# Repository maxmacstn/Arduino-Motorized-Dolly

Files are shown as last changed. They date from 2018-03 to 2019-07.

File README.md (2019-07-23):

# Arduino-Motorized-Dolly
Convert generic camera dolly rail into controllable motorized dolly.

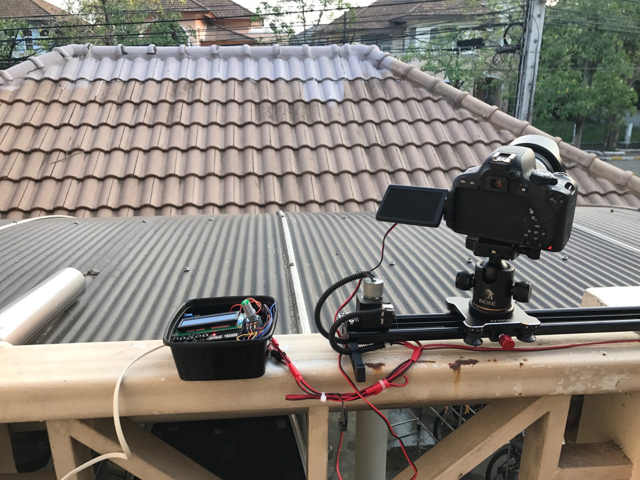
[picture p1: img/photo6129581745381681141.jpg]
Arduino Dolly


## Features
- 5v powerbank input (Portable!)
- Adjustable speed.
- Video mode (Continuous movement)
- TimeLapse mode with camera shutter trigger.
- Can be set Timelapse delay time (time for camera to save image between shot), Motor position (Left or right of the controller) and Time until display is going to dim. Those are available in Settings menu and the configuration will be stored in the EEPROM which means that configuration still remains after power lost.

## Main Components
1. Andoer 80cm / 32" 4 Bearings Camera Slider
2. Arduino Mega 2560
3. Gear motor 12v 50RPM
4. Arduino Modules
    1. L298N H-Bridge motor driver
    2. LCD Keypad shield
    3. DC-to-DC Step Up XL6009
    4. Limit switch ×2
5. Belt components
    1. timing GT2 belt width 6mm
    2. Timing Pulley 20 ฟัน 2GT 
    3. Pulley Wheel 20 ฟัน 2GT
    4. Timing Belt Fixing Clamp 9*40mm
6. Shutter trigger components
    1. NPN Transistor BC547
    2. Resistor 1K Ω
    3. 2.5mm female headphone jack

## Schematic
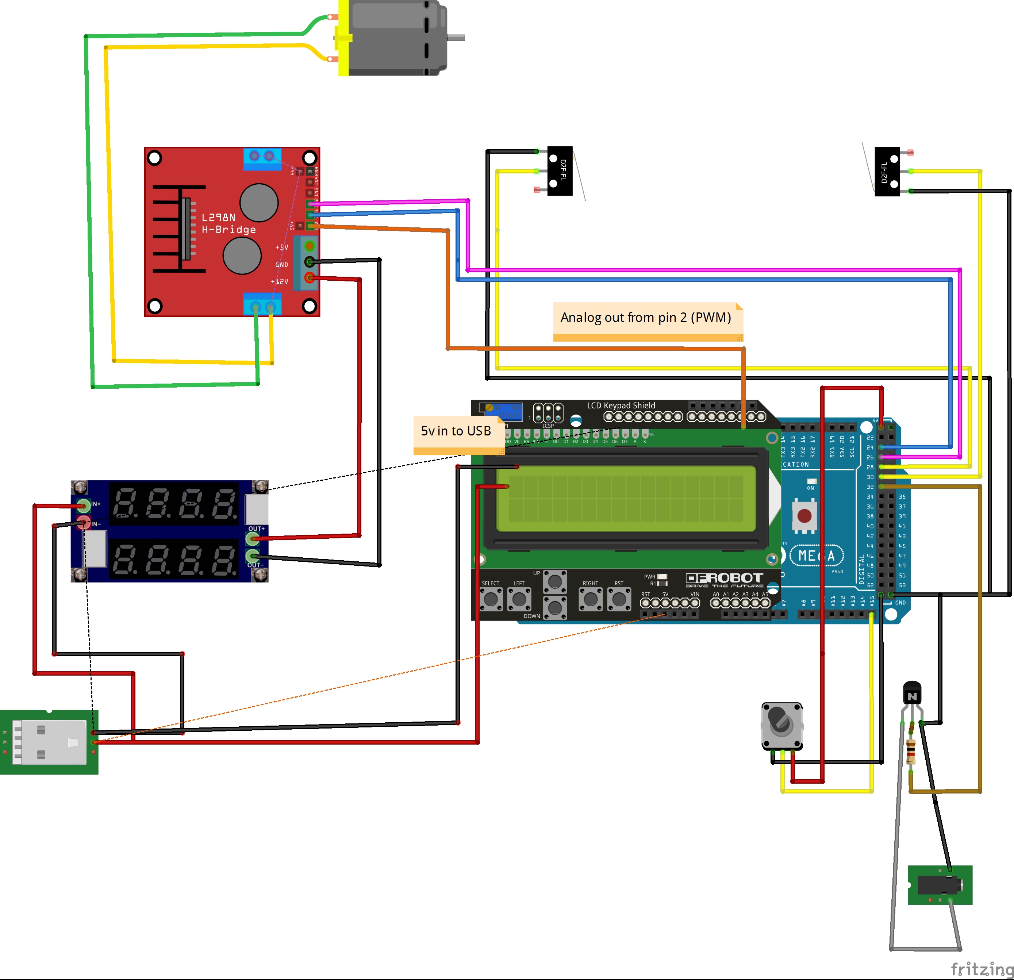
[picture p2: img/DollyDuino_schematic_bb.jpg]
Schematic

 **Pins** (Pin number : variable name - Description)
 - 2 : enA - PWM Motor control 
 - 24 : in1 - Motor rotational  control 1
 - 26 : in2 - Motor rotational control 2
 - 28 : limSW_L - Left limit switch
 - 30 : limSW_R - Right limit switch
 - 32 : shutter - Camera shutter trigger pin
 Those below pins are connected via LCD Keypad shield
  - 0 : btnRIGHT  
  - 1 : btnUP 
  - 2 : btnDOWN 
  - 3 : btnLEFT
  - 4 :btnSELECT
  - 5 : btnNONE 
  - 10 : brightnessPin - PWM-controlled brightness of LCD Backlight

## Dependencies
- LiquidCrystal.h
- EEPROM.h

## Link
- [Youtube Link](https://youtu.be/vfO5Gkq3VD4)
- [Blog(Thai)](https://maxmacstn.wordpress.com/2018/03/09/dollyduino/)

## V.2 Update
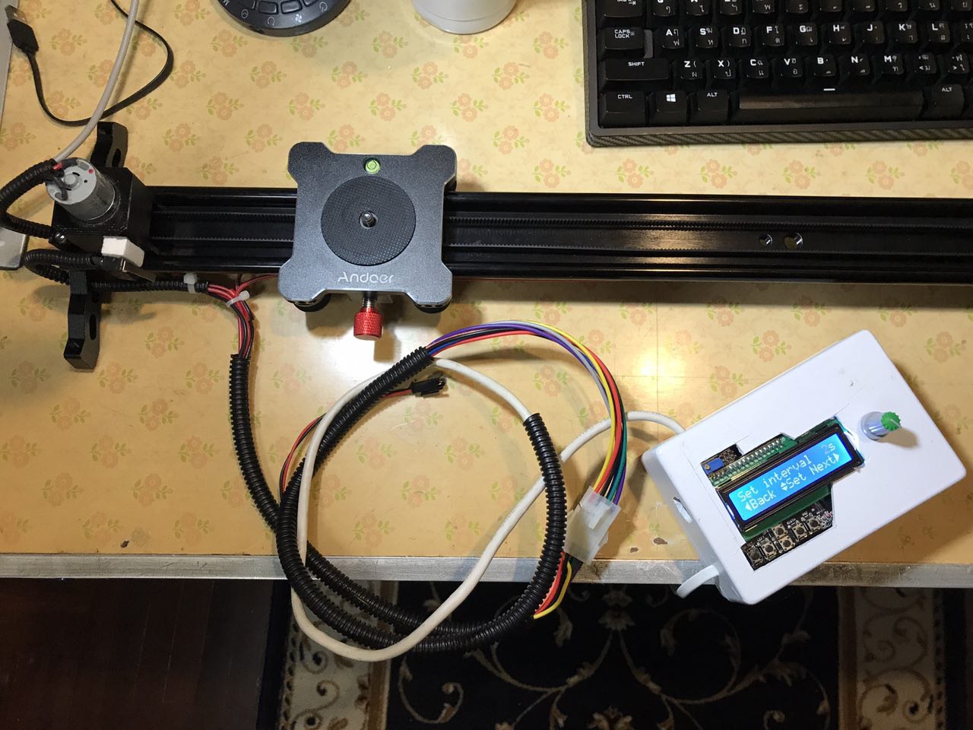
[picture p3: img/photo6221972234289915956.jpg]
Arduino Dolly V.2


-	New nice and tidy Arduino enclosure ([Box from FutureKit : Size FB-04](https://www.futurekit.com/product/25654/fb04))
  You can see how all of the components are perfectly fit in that box from [here](https://github.com/maxmacstn/Arduino-Motorized-Dolly/blob/master/img/photo6221972234289915957.jpg)
-	9 Pins connector, really convenient! 
-	Software upgrade.

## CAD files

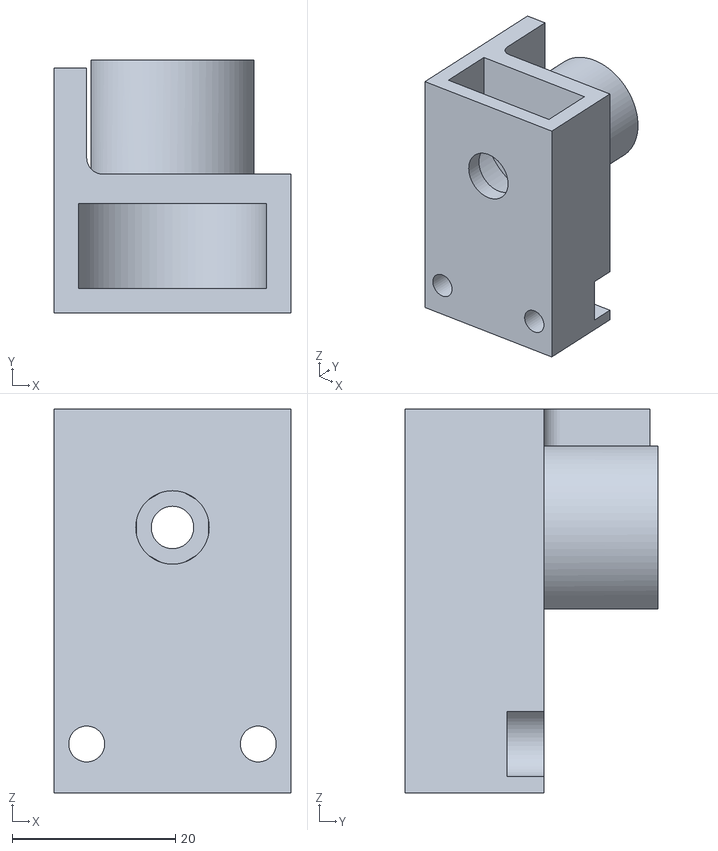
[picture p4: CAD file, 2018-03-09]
3D Files/Belt_holder.stl
29.0 x 31.0 x 47.0

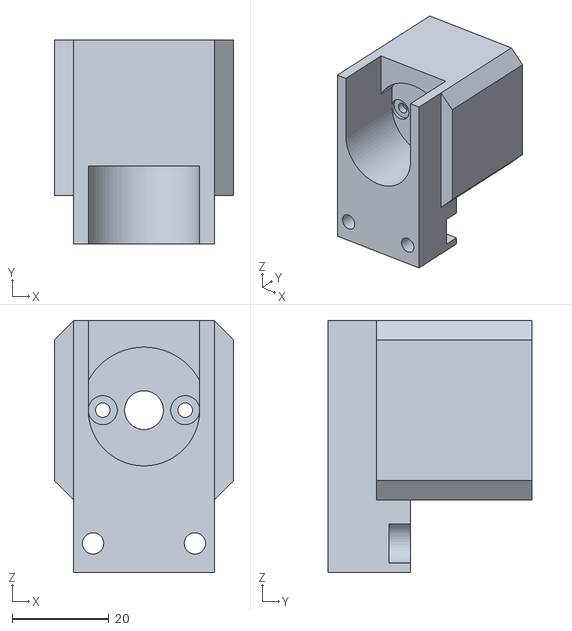
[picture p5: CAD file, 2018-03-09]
3D Files/Motor_holder.stl
37.0 x 42.0 x 52.0

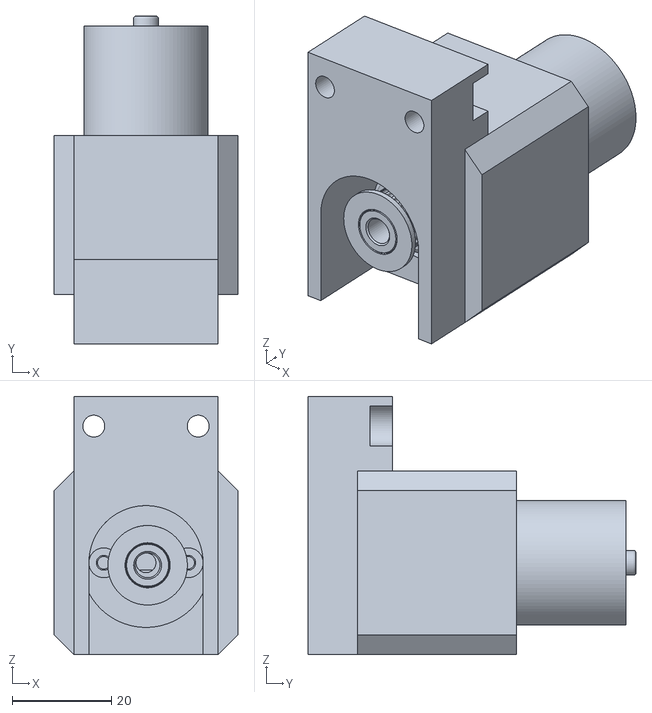
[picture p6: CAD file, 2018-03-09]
3D Files/Motor_holder_with_motor.stl
37.0 x 66.0 x 52.0

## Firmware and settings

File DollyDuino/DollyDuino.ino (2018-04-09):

/**
    @file    DollyDuino
    @author  Sitinut Waisara (maxmacstn)
    @date    April,7 2018
    @version 2.0

    Automated camera dolly control using Arduino.
    https://github.com/maxmacstn/Arduino-Motorized-Dolly
    https://maxmacstn.wordpress.com/2018/03/09/dollyduino/


*/


#include <LiquidCrystal.h>
#include <EEPROM.h>

LiquidCrystal lcd(8, 9, 4, 5, 6, 7);

#define enA 2                       //PWM Motor control
#define in1 24                      //Motor rotational control1
#define in2 26                      //Motor rotational control2
#define limSW_L 28                  //Left limit switch
#define limSW_R 30                  //Right limit switch
#define shutter 32                  //Camera shutter trigger pin
#define btnRIGHT  0 
#define btnUP     1
#define btnDOWN   2
#define btnLEFT   3
#define btnSELECT 4
#define btnNONE   5
#define brightnessPin 10            //LCD Brightness control (Connected from the LCD Keypad shield)


const char* menuItems[] = {"     VIDEO             ", "   TIMELAPSE           ", "    SETTINGS   "};
const unsigned int menuItemsNumber = 3;
const unsigned int sleepTime[] = {0, 10, 30, 120, 300};
unsigned long lastActiveTime = 0;
byte lastPotValue = 255;
byte currentBrightness = 255;
byte motorDir = 0;     // positive = motor is on the left of the controller
byte cameraDelay = 0;  //camera delay between shots (Seconds)
byte dimChoice = 0;    //choice of time until screen was dim.

byte updn_arrow[] = {
  B00100,
  B01110,
  B11111,
  B00000,
  B11111,
  B01110,
  B00100,
  B00000
};

byte left_arrow[] = {

  B00010,
  B00110,
  B01110,
  B11110,
  B01110,
  B00110,
  B00010,
  B00000
};

byte right_arrow[] = {
  B10000,
  B11000,
  B11100,
  B11110,
  B11100,
  B11000,
  B10000,
  B00000
};

byte move_left[] = {
  B00010,
  B00100,
  B01000,
  B10000,
  B01000,
  B00100,
  B00010,
  B00000
};

byte move_right[] = {
  B01000,
  B00100,
  B00010,
  B00001,
  B00010,
  B00100,
  B01000,
  B00000
};



// define some values used by the panel and buttons
int lcd_key     = 0;
int adc_key_in  = 0;
volatile int rotDirection = 0;
int pressed = false;

// read the buttons
int read_LCD_buttons()
{
  adc_key_in = analogRead(0);      // read the value from the sensor
  // my buttons when read are centered at these valies: 0, 144, 329, 504, 741
  // we add approx 50 to those values and check to see if we are close
  if (adc_key_in > 1000) return btnNONE; // We make this the 1st option for speed reasons since it will be the most likely result
  // For V1.1 us this threshold
  resetDisplaySleep();

  if (adc_key_in < 50)   return btnRIGHT;
  if (adc_key_in < 250)  return btnUP;
  if (adc_key_in < 450)  return btnDOWN;
  if (adc_key_in < 650)  return btnLEFT;
  if (adc_key_in < 850)  return btnSELECT;

  return btnNONE;  // when all others fail, return this...
}

void video_mode() {
  lcd.clear();
  lcd.setCursor(3, 0);
  lcd.print("Speed");
  lcd.setCursor(0, 1);
  lcd.write((byte)0);
  lcd.setCursor(1, 1);
  lcd.print("stop");

  resetDisplaySleep();
  checkDisplaySleep();
  bool dir;

  while (1) {

    int potValue = analogRead(A15); // Read potentiometer value
    int pwmOutput = map(potValue, 0, 1023, 0 , 255); // Map the potentiometer value from 0 to 255
    int pwmPercent = map(potValue, 0, 1023, 0, 100); // Map pot to percent for display
    Serial.println(potValue);
    analogWrite(enA, pwmOutput); // Send PWM signal to L298N Enable pin

    // Check limit switch - Debounce
    if (!digitalRead(limSW_L)) {
      rotDirection = 1;
    }
    if (!digitalRead(limSW_R)) {
      rotDirection = 0;
    }
    if (read_LCD_buttons() == btnLEFT) {
      digitalWrite(in1, LOW);
      digitalWrite(in2, LOW);
      lcd.clear();
      return;
    }
    if (read_LCD_buttons() == btnSELECT) {
      while (read_LCD_buttons() == btnSELECT) {}
      rotDirection = !rotDirection;
    }
    delay(20);
    // If button is pressed - change rotation direction
    if (rotDirection == 0) {
      digitalWrite(in1, HIGH);
      digitalWrite(in2, LOW);
      delay(20);
    }
    // If button is pressed - change rotation direction
    if (rotDirection == 1) {
      digitalWrite(in1, LOW);
      digitalWrite(in2, HIGH);
      delay(20);
    }

    //Update LCD
    if (pwmPercent >= 100) {
      lcd.setCursor(9, 0);
      lcd.print(pwmPercent);
    }
    else if (pwmPercent >= 10) {
      lcd.setCursor(9, 0);
      lcd.print(" ");
      lcd.setCursor(10, 0);
      lcd.print(pwmPercent);

    } else {
      lcd.setCursor(9, 0);
      lcd.print("  ");
      lcd.setCursor(11, 0);
      lcd.print(pwmPercent);
    }

    lcd.setCursor(12, 0);
    lcd.print("%");

    lcd.setCursor(0, 0);
    lcd.print("   ");
    lcd.setCursor(13, 0);
    lcd.print("   ");

    //Arrow animation speed.
    int anim_shift = millis() / 1000 % 3;

    if (pwmPercent >= 90) {
      anim_shift = millis() / 500 % 3;
    }

    if (pwmPercent <= 40) {
      anim_shift = millis() / 1500 % 3;
    }
    if (pwmPercent <= 10) {
      anim_shift = millis() / 2500 % 3;
    }

    dir = rotDirection;
    if (motorDir)
      dir = !dir;

    if (!dir) {    //Motor is on the left
      lcd.setCursor(2 - anim_shift, 0);
      lcd.write((byte)3);
    }
    else {
      lcd.setCursor(13 + anim_shift, 0);
      lcd.write((byte)4);
    }

    checkDisplaySleep();

  }
}

//Load user-saved settings from EEPROM into global variable
void loadSaveData() {
  byte loadedMotorDir = EEPROM.read(0);
  byte loadedCameraDelay = EEPROM.read(1);
  byte loadedDimChoice = EEPROM.read(2);

  // Reset EEPROM Value to 0 if the loaded value is not valid.
  if ( loadedMotorDir > 1) {
    loadedMotorDir = 0;
    EEPROM.write(0, 0);
  }
  if ( loadedCameraDelay > 20) {
    loadedCameraDelay = 0;
    EEPROM.write(1, 0);
  }

  if ( loadedDimChoice > 4) {
    loadedDimChoice = 0;
    EEPROM.write(2, 0);
  }

  motorDir = loadedMotorDir;
  cameraDelay = loadedCameraDelay;
  dimChoice = loadedDimChoice;
}

void setup() {
  pinMode(enA, OUTPUT);
  pinMode(in1, OUTPUT);
  pinMode(in2, OUTPUT);
  pinMode(shutter, OUTPUT);

  // Init Limit sensor and set built-in pullup
  pinMode(limSW_L, INPUT);
  pinMode(limSW_R, INPUT);
  digitalWrite(limSW_L, HIGH);
  digitalWrite(limSW_R, HIGH);

  // Set initial rotation direction
  digitalWrite(in1, LOW);
  digitalWrite(in2, HIGH);

  pinMode(brightnessPin, OUTPUT);
  digitalWrite(brightnessPin, HIGH);

  //Serial.begin(9600);

  //Create custom characters
  lcd.createChar(0, left_arrow);
  lcd.createChar(1, right_arrow);
  lcd.createChar(2, updn_arrow);
  lcd.createChar(3, move_left);
  lcd.createChar(4, move_right);

  //init led screen
  lcd.begin(16, 2);              // start the library
  lcd.clear();
  lcd.setCursor(0, 0);
  lcd.print(" DollyDuino 2.0"); // print a Welcome message
  lcd.setCursor(3, 1);
  lcd.print("Starting...."); // print a Welcome message
  loadSaveData();
  delay(1000);
}

void loop() {
  lcd.clear();
  lcd.setCursor(3, 0);
  lcd.print("Main Menu");
  int currentMenu = 0;
  lcd.setCursor(0, 1);
  lcd.print(menuItems[0]);
  Serial.println("MainLoop");
  lcd.setCursor(15, 1);
  lcd.write((byte)1);
  resetDisplaySleep();
  while (1) {
    if (read_LCD_buttons() == btnRIGHT && currentMenu != menuItemsNumber - 1 ) {
      while (read_LCD_buttons() == btnRIGHT) {};
      update_lcd_menu(currentMenu + 1, true);
      currentMenu++;

    }
    if (read_LCD_buttons() == btnLEFT && currentMenu != 0) {
      while (read_LCD_buttons() == btnLEFT) {};
      update_lcd_menu(currentMenu - 1, false);
      currentMenu--;
    }
    if (read_LCD_buttons() == btnSELECT) {
      while (read_LCD_buttons() == btnSELECT) {};
      switch (currentMenu) {
        case 0: video_mode(); break;
        case 1: time_lapse(); break;
        case 2: setting_page(); break;
      }
      break;
    }

    checkDisplaySleep();

  }




}

void update_lcd_menu(int targetMenu, boolean isIncrement) {
  checkDisplaySleep();

  int scroll_speed = 10;

  //Text scroll animation
  if (isIncrement == true) {                  //Right to left
    //Move previous text out of screen
    for (int i = 0; i > -16; i--) {

      lcd.setCursor(0, 1);
      //lcd.print("                ");
      lcd.setCursor(i, 1);
      lcd.print(menuItems[targetMenu - 1]);
      delay(scroll_speed);
    }
    for (int i = 16; i >= 0; i--) {
      lcd.setCursor(0, 1);
      //lcd.print("                ");
      lcd.setCursor(i, 1);
      lcd.print(menuItems[targetMenu]);
      delay(scroll_speed);
    }
  }
  else {                                      //Left to right
    //Move previous text out of screen
    for (int i = 0; i < 16; i++) {
      lcd.setCursor(0, 1);
      //lcd.print("                ");
      lcd.setCursor(i, 1);
      lcd.print(menuItems[targetMenu + 1]);
      delay(scroll_speed);
    }
    for (int i = -16; i <= 0; i++) {
      lcd.setCursor(0, 1);
      //lcd.print("                ");
      lcd.setCursor(i, 1);
      lcd.print(menuItems[targetMenu]);
      delay(scroll_speed);
    }

  }

  //Draw arrow
  if (targetMenu != 0) {
    lcd.setCursor(0, 1);
    lcd.write((byte)0);
  }
  if (targetMenu != menuItemsNumber - 1) {
    lcd.setCursor(15, 1);
    lcd.write((byte)1);
  }

  return;

}


void time_lapse() {
  resetDisplaySleep();
  checkDisplaySleep();
  lcd.clear();
  byte int_sec = 1;
  int step_sec = 500;
  while (1) {
    lcd.setCursor(0, 0);
    lcd.print("Set interval");
    lcd.setCursor(15, 0);
    lcd.print("s");
    lcd.setCursor(0, 1);
    lcd.write((byte)0);
    lcd.setCursor(1, 1);
    lcd.print("Back");

    lcd.setCursor(6, 1);
    lcd.write((byte)2);
    lcd.setCursor(7, 1);
    lcd.print("Set");

    lcd.setCursor(11, 1);
    lcd.print("Next");
    lcd.setCursor(15, 1);
    lcd.write((byte)1);
    boolean value_update = false;
    if (read_LCD_buttons() == btnUP) {
      while (read_LCD_buttons() == btnUP) {}
      if (int_sec < 100) {
        int_sec++;
        value_update = true;
      }
    }
    if (read_LCD_buttons() == btnDOWN) {
      while (read_LCD_buttons() == btnDOWN) {}
      if (int_sec > 1) {
        int_sec--;
        value_update = true;
      }
    }
    if (read_LCD_buttons() == btnLEFT) {
      lcd.clear();
      return;
    }

    //Blink and update LCD
    if (millis() % 1000 > 500 || value_update == true) {
      if (int_sec >= 10) {
        lcd.setCursor(13, 0);
      }
      else {
        lcd.setCursor(13, 0);
        lcd.print(" ");
        lcd.setCursor(14, 0);
      }
      lcd.print(int_sec);
    }
    else {
      lcd.setCursor(13, 0);
      lcd.print("  ");
    }

    //Continue to step 2
    if (read_LCD_buttons() == btnRIGHT) {
      lcd.clear();
      while (read_LCD_buttons() == btnRIGHT) {};
      while (1) {
        lcd.setCursor(0, 0);
        lcd.print("Set move");
        lcd.setCursor(14, 0);
        lcd.print("ms");
        lcd.setCursor(0, 1);
        lcd.write((byte)0);
        lcd.setCursor(1, 1);
        lcd.print("Back");

        lcd.setCursor(6, 1);
        lcd.write((byte)2);
        lcd.setCursor(7, 1);
        lcd.print("Set");

        lcd.setCursor(12, 1);
        lcd.print("Run");
        lcd.setCursor(15, 1);
        lcd.write((byte)1);
        boolean value_update = false;
        if (read_LCD_buttons() == btnUP) {
          while (read_LCD_buttons() == btnUP) {}
          if (step_sec < 9000) {
            step_sec += 100;
            value_update = true;
          }
        }
        if (read_LCD_buttons() == btnDOWN) {
          while (read_LCD_buttons() == btnDOWN) {}
          if (step_sec > 100) {
            step_sec -= 100;
            value_update = true;
          }
        }

        //Blink and update LCD
        if (millis() % 1000 > 500 || value_update == true) {
          if (step_sec >= 1000) {
            lcd.setCursor(10, 0);
          }
          else {
            lcd.setCursor(10, 0);
            lcd.print("   ");
            lcd.setCursor(11, 0);
          }
          lcd.print(step_sec);
        }
        else {
          lcd.setCursor(10, 0);
          lcd.print("    ");
        }
        if (read_LCD_buttons() == btnLEFT) {
          while (read_LCD_buttons() == btnLEFT) {};
          lcd.clear();
          break;
        }
        if (read_LCD_buttons() == btnRIGHT) {
          lcd.clear();
          do_timeLapse(int_sec + cameraDelay, step_sec);
        }
        checkDisplaySleep();

      }
      checkDisplaySleep();

    }//End step2
    checkDisplaySleep();
  }

}

void do_timeLapse(char int_sec, int step_sec) {
  unsigned long startShootMillis = 0;
  unsigned long startMoveMillis = 0;
  boolean isShot = false;
  boolean isShooting = false;
  boolean isFirstEnter = true;
  unsigned int shotCount = 0;
  lcd.setCursor(0, 0);
  lcd.print("TimeLapse");
  lcd.setCursor(13, 0);
  lcd.print("img");
  lcd.setCursor(0, 1);
  lcd.write((byte)0);
  lcd.setCursor(1, 1);
  lcd.print("Stop");

  resetDisplaySleep();
  checkDisplaySleep();

  while (1) {
    lcd.setCursor(10, 0);
    lcd.print(shotCount);
    int potValue = analogRead(A15); // Read potentiometer value
    int pwmOutput = map(potValue, 0, 1023, 0 , 255); // Map the potentiometer value from 0 to 255
    unsigned long currentMillis = millis();
    Serial.println(potValue);
    analogWrite(enA, pwmOutput); // Send PWM signal to L298N Enable pin

    // Check limit switch - Debounce
    if (!digitalRead(limSW_L)) {
      rotDirection = 1;
    }
    if (!digitalRead(limSW_R)) {
      rotDirection = 0;
    }
    if (read_LCD_buttons() == btnLEFT) {
      digitalWrite(in1, LOW);
      digitalWrite(in2, LOW);
      lcd.clear();
      return;
    }
    Serial.print("startShootMillis = ");
    Serial.println(startShootMillis);
    Serial.print("startMoveMillis = ");
    Serial.println(startMoveMillis);
    Serial.print("CurrentMillis = ");
    Serial.println(currentMillis);

    // exceed delay time of move
    if (currentMillis - startMoveMillis >= step_sec) {
      Serial.println("Exceed move time");
      digitalWrite(in1, LOW);
      digitalWrite(in2, LOW);
      if (isFirstEnter == true) {
        startShootMillis = millis();
        currentMillis = millis();
        isFirstEnter = false;
      }
      // exceed delay time of shooting
      if (currentMillis - startShootMillis  >= int_sec * 1000) {
        startMoveMillis = millis();
        Serial.println("Exceed shoot time ...................");
        Serial.println(startShootMillis -  currentMillis);
        isFirstEnter = true;
        isShot = true;

      } else if (isShot == true) {
        delay(100);
        digitalWrite(shutter, HIGH);
        delay(100);
        digitalWrite(shutter, LOW);
        isShot = false;
        shotCount++;
      }

    } else {  // Move motor
      if (rotDirection == 0) {
        digitalWrite(in1, HIGH);
        digitalWrite(in2, LOW);
        // delay(20);
      }
      // If button is pressed - change rotation direction
      if (rotDirection == 1) {
        digitalWrite(in1, LOW);
        digitalWrite(in2, HIGH);
        //delay(20);
      }

      checkDisplaySleep();
    }
    checkDisplaySleep();
  }
}

void setting_page() {
  lcd.clear();
  byte newMotorDir = motorDir;
  while (1) {
    lcd.setCursor(0, 0);
    lcd.print("Motor pos.");




    lcd.setCursor(0, 1);
    lcd.write((byte)2);
    lcd.setCursor(1, 1);
    lcd.print("Set");

    lcd.setCursor(11, 1);
    lcd.print("Next");
    lcd.setCursor(15, 1);
    lcd.write((byte)1);
    boolean value_update = false;
    if (read_LCD_buttons() == btnUP || read_LCD_buttons() == btnDOWN ) {
      while (read_LCD_buttons() == btnUP || read_LCD_buttons() == btnDOWN) {}
      newMotorDir = !newMotorDir;
      value_update = true;

    }
    if (read_LCD_buttons() == btnLEFT) {
      lcd.clear();
      return;
    }

    //Blink and update LCD
    if (millis() % 1000 > 500 || value_update == true) {
      lcd.setCursor(11, 0);
      if (newMotorDir == 0)
        lcd.print("LEFT ");
      else
        lcd.print("RIGHT");
    }
    else {
      lcd.setCursor(11, 0);
      lcd.print("     ");
    }

    //Continue to step 2
    if (read_LCD_buttons() == btnRIGHT) {
      lcd.clear();
      byte newValue = cameraDelay;
      while (read_LCD_buttons() == btnRIGHT) {};
      while (1) {
        lcd.setCursor(0, 0);
        lcd.print("TL. Delay");
        lcd.setCursor(15, 0);
        lcd.print("s");



        lcd.setCursor(0, 1);
        lcd.write((byte)2);
        lcd.setCursor(1, 1);
        lcd.print("Set");

        lcd.setCursor(11, 1);
        lcd.print("Next");
        lcd.setCursor(15, 1);
        lcd.write((byte)1);
        boolean value_update = false;

        if (read_LCD_buttons() == btnUP) {
          while (read_LCD_buttons() == btnUP) {}
          if (newValue < 20)
            newValue++;
          value_update = true;
        }
        if (read_LCD_buttons() == btnDOWN) {
          while (read_LCD_buttons() == btnDOWN) {}
          if (newValue > 0)
            newValue--;
        }

        //Blink and update LCD
        if (millis() % 1000 > 500 || value_update == true) {
          lcd.setCursor(12, 0);
          lcd.print(newValue);
        }
        else {
          lcd.setCursor(12, 0);
          lcd.print("   ");
        }

        //set Auto Dim
        if (read_LCD_buttons() == btnRIGHT) {
          while (read_LCD_buttons() == btnRIGHT) {}
          lcd.clear();
          lcd.setCursor(0, 0);
          lcd.print("Screen dim");
          lcd.setCursor(15, 0);
          lcd.print("s");



          lcd.setCursor(0, 1);
          lcd.write((byte)2);
          lcd.setCursor(1, 1);
          lcd.print("Set");

          lcd.setCursor(11, 1);
          lcd.print("SAVE");
          lcd.setCursor(15, 1);
          lcd.write((byte)1);
          int newDimChoice = dimChoice;

          while (1) {
            boolean value_update = false;
            if (read_LCD_buttons() == btnUP) {
              while (read_LCD_buttons() == btnUP) {}
              if (newDimChoice < 4)
                newDimChoice++;
              value_update = true;
            }
            if (read_LCD_buttons() == btnDOWN) {
              while (read_LCD_buttons() == btnDOWN) {}
              if (newDimChoice > 0)
                newDimChoice--;
            }

            //Blink and update LCD
            if (millis() % 1000 > 500 || value_update == true) {
              lcd.setCursor(12, 0);
              if (!newDimChoice){
                lcd.print("--");
              }
              else
                lcd.print(sleepTime[newDimChoice]);
            }
            else {
              lcd.setCursor(12, 0);
              lcd.print("   ");
            }

            if (read_LCD_buttons() == btnRIGHT) {
              while (read_LCD_buttons() == btnRIGHT) {}
              lcd.clear();
              EEPROM.write(0, newMotorDir);
              EEPROM.write(1, newValue);
              EEPROM.write(2, newDimChoice);
              motorDir = newMotorDir;
              cameraDelay = newValue;
              dimChoice = newDimChoice;
              lcd.setCursor(5, 0);
              lcd.print("Saved!");
              delay(1000);
              return;
            }
            checkDisplaySleep();

          }
        }
        checkDisplaySleep();
      }
      checkDisplaySleep();
    }//End step2
    checkDisplaySleep();
  }
}

void checkDisplaySleep() {
  if (dimChoice == 0){
    analogWrite(brightnessPin, 255);
    return;
  }
  int potValue = analogRead(A15); // Read potentiometer value
  int pwmOutput = map(potValue, 0, 1023, 0 , 255); // Map the potentiometer value from 0 to 255

  if (abs(pwmOutput - lastPotValue) > 5) {
    lastPotValue = pwmOutput;
    resetDisplaySleep();
  }

  if (millis() - lastActiveTime > sleepTime[dimChoice] * 1000){
    for (int i = currentBrightness; i >=10 ; i--){
       analogWrite(brightnessPin, i);
       delay(1);

    }
    currentBrightness = 10;
  }
  else {
    for (int i = currentBrightness; i <= 255 ; i++){
       analogWrite(brightnessPin, i);
       delay(1);

    }
    currentBrightness = 255;
  }


}

void resetDisplaySleep() {
  lastActiveTime = millis();
}
